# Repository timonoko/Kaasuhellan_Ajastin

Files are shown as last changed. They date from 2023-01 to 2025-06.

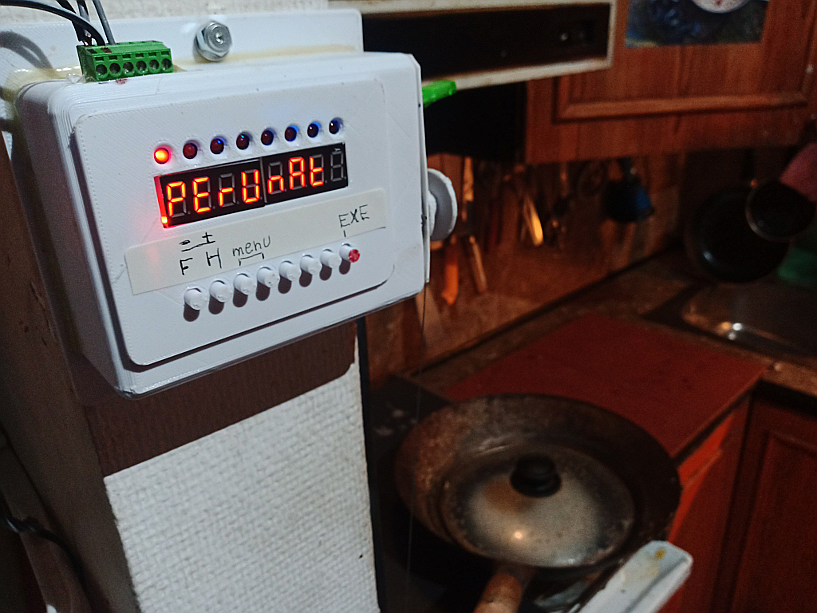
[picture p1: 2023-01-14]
Perunat.png

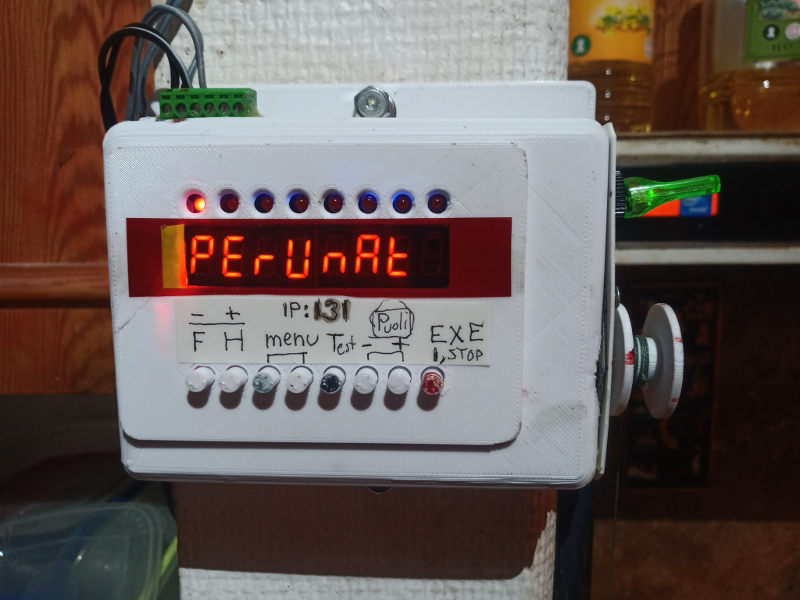
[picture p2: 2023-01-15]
perunat2.png

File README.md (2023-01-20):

# Kaasuhellan_Ajastin

ESP32-vehje kelaa siimalla vipuvarren päässä olevaa lieden pääkatkaisinta. Säätää
myös puoliliekin.

Havaitsee palohälytyksen, koska palohälyttimessä oleva transistori vetää
kun kaijuttimesta tulee ääntä.

Vehkeessä on myös eri ruokalajeille viritetty menyy.

Askelmoottori on entisestä skannerista ja näyttönappimoduuli on TM1638.

Mitään raja-antureita ei ole, sillä kun virrat katkaistaan, painovoima vetää rullauskelan takasin nolla-asentoon.
Kytkin myös A4988:n enable-pinnin, niin että toiminnan alussa vipua nostetaan 50 pykälää ja annetaan
sen jälkeen vapaasti pudota, jolloin nollaus on tarkka.

Hellan yläpuolella oleva lämpömittari TMP36GT9Z sammuttaa hanan, jos lämpötila on yli MAX_TEMP -- tai kun keittämistaä on kestänyt yli 3 minuuttia ja lämpötila on silti alle MIN_TEMP.

https://youtu.be/Kd3liw780tA

<image src=xstop.png>
<image src=Perunat.png>

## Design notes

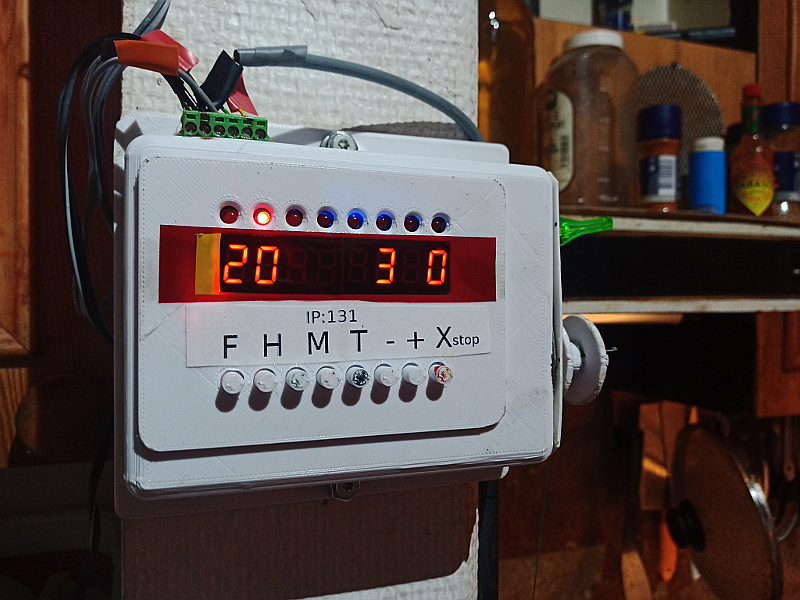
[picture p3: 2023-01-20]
xstop.png

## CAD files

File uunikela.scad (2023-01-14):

$fn=100;

difference(){
  cylinder(d=30,h=14);
  translate([0,0,-1])cylinder(d=7.2,h=17);
   translate([0,0,2]) difference(){
    cylinder(d=32,h=10);
    translate([0,0,-1])cylinder(d=12,h=17);
   }
}

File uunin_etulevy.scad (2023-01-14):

include <roundedcube.scad>


$fn=80;
thei=6.5;
module tappi(th) {
  difference(){
    cylinder(d=5.5,h=th);
    translate([0,0,-1]) cylinder(d=2.5,h=10+th);
  }
}
module etulevy () {
  difference() {
  translate([-10,-10,0])cube([76.5+20,50+20,2]);
  //  cube([76.5,50,2]);
  for (x=[10.5:56/7:67])translate([x,50-3.5,-1])cylinder(d1=3,d2=8,h=4);
  for (x=[11.2:54.45/7:67])translate([x,5.8,-1])cylinder(d=6,h=4);
  translate([6.5,27,-1]) cube([63,15,4]);
  translate([1,11,-1])  cube([3,13,2.5]);
  }
  translate([4,5,-thei])tappi(thei);
  translate([76.5-4,5,-thei])tappi(thei);
  translate([4,50-4.5,-thei])tappi(thei);
  translate([76.5-4,50-4.5,-thei])tappi(thei);
}


module nappaimet () { 
  for (x=[11.2:54.45/7:67])translate([x,5.8,0])cylinder(d=5,h=8);
  for (x=[11.2:54.45/7:67])translate([x,5.8,0])cylinder(d=7,h=1);
  for (x=[11.2:54.45/7:67])translate([x-2,5.8,0])cube([4,20,1]);
  translate([9,22,0])cube([60,5,1]);
}


module kotelo () {
  difference() {
    roundedcube([120,90,50],radius=6);
    translate([2,2,2])roundedcube([116,86,46],radius=4);
    translate([0,0,-1])cube([120,92,11]);
    translate([14,20,0]) cube([80,60,60]);
    translate([110,30,30])rotate([0,90,0])cylinder(d=36,h=20);
    translate([105,35,20])cube(18);
  }
  translate([4.5,4.5,12])tappi(35);
  translate([120-4.5,4.5,12])tappi(35);
  translate([120-4.5,90-4.5,12])tappi(35);
  translate([4.5,90-4.5,12])tappi(35);
}

module kansi () {
  difference() {
    union (){
      difference() {
	translate([2.3,2.3,0])roundedcube([115.4,85.4,46],radius=3.4);
	translate([0,0,-1])cube([120,92,5]);
	translate([0,0,7])cube([120,92,50]);
      }
      translate([0,0,-3])difference() {
	translate([-5,-15,0])roundedcube([130,120,46],radius=3.4);
	translate([-10,-17,-1])cube([170,130,5]);
	translate([-10,-17,7])cube([170,130,50]);
      }
    }
    translate([4.5,4.5,-2])cylinder(d=3,h=10);
    translate([120-4.5,4.5,-2])cylinder(d=3,h=10);
    translate([120-4.5,90-4.5,-2])cylinder(d=3,h=10);
    translate([4.5,90-4.5,-2])cylinder(d=3,h=10);
    translate([8,8,-2])roundedcube([104,74,46],radius=4);
  }
}

//translate([-10,-10,2]) rotate([180,0,0]) color("RED") etulevy(); nappaimet();

//translate([16,25,50]) etulevy();
//kotelo();
kansi();

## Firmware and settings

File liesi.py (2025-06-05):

# Kaasukeittiön totaalinen haltuunotto (c) Tnoko 2023

import tm1638,time,machine
from machine import Pin

tm = tm1638.TM1638(stb=Pin(13), clk=Pin(14), dio=Pin(12))

palohaly=Pin(15,Pin.IN)

direction=Pin(27,Pin.OUT)
step=Pin(17,Pin.OUT)
stepable=Pin(5,Pin.OUT)

adc=machine.ADC(machine.Pin(33),atten=machine.ADC.ATTN_11DB)

def tempe1():
    return (adc.read()*2450/900)*100./4096-50.

TEMP=tempe1()

def tempera(): # Kohinainen lämpomittari, käytetään 10 otoksen keskiarvoa
    global TEMP
    TEMP=(99*TEMP+tempe1())/100
    return 24+int(TEMP)

tempera();tempera();tempera()

MIN_TEMP_ORIG=tempera()
if MIN_TEMP_ORIG>25: MIN_TEMP_ORIG=25
MIN_TEMP=MIN_TEMP_ORIG
MIN_TEMP_TIME=5
MAX_TEMP=45

tm.brightness(1)
UP=1
DOWN=0
SIJAINTI=0

def myscroll(x):
      tm.show('        ')
      if len(x)<9: tm.show(x)
      else:
        x='  '+x
        for i in range(0,len(x)-7):
             tm.show(x[i:(i+8)])
             time.sleep(0.2)

def kaasuhana(asento,speed=500):
    global SIJAINTI
    tm.brightness(7)
    steps=asento-SIJAINTI
    if steps==0: return
    if steps<0: suunta=DOWN
    else: suunta=UP
    print('steps,suunta=',steps,suunta)
    direction.value(suunta)
    for x in range(abs(steps)):
        if suunta==UP: SIJAINTI+=1
        else: SIJAINTI-=1
        tm.number(SIJAINTI)
        tm.leds(x)
        step.value(1)
        time.sleep(1/speed)
        step.value(0)
        time.sleep(1/speed)
#    time.sleep(1)
    tm.brightness(1)
    with open('SIJAINTI.TXT', 'w') as f:  f.write('%d' % SIJAINTI)

from MENYY import menyy

def valinta(v):
    time.sleep(0.2)
    while True:
        tm.leds(2**v)
        myscroll(menyy[v][0])
        while True:
            k=tm.keys()
            if k>0:
                break
        time.sleep(0.3)
        if k==2**3:
            v=v+1
            if v==len(menyy):
                v=0
        if k==2**2:
            v=v-1
            if v<0:
                v=len(menyy)-1
        if k==2**7:
            break
    return v

def keys01(k):
    global aika1,aika2
    if k==2**0:
        if aika1==0:  aika1=1
        else: aika1=round(aika1*1.5)
        if aika1>500:  aika1=0
    if k==2**1:
        if aika2==0: aika2=1
        else: aika2=round(aika2*1.5)
        if aika2>500: aika2=0
    cou=0
    while tm.keys()>0:
        time.sleep(0.1)
        cou+=1
        if cou>3:
            if k==2**0: aika1=1
            if k==2**1: aika2=0

def hienosaato(k):  # Puoliliekin hienosäätö
    global PUOLI
    if k==2**5: PUOLI-=1
    else: PUOLI+=1
    puoli()
    tm.number(PUOLI)
    with open('PUOLI.TXT', 'w') as f:
        f.write('%d' % PUOLI)
    time.sleep(1)

def showtime (aika1, aika2):
    s=str(aika1)+" "+str(aika2)
    if MIN_TEMP==tempera(): s="E "+s
    elif MIN_TEMP>tempera(): s="- "+s
    while len(s)<6: s=" "+s
    tm.show(str(tempera())+s)

VIESTI=""
def keitto(kypalla): 
    global AIKA,MIN_TEMP_TIME,aika1,aika2,MIN_TEMP,VIESTI
    if kypalla: minsaa=aika1
    else: minsaa=aika2
    while minsaa > 0:
        for y in range(6):
            if y==4 and MIN_TEMP==100:  myscroll("SAMMUTA KATTILA")
            for z in range(10):
                tm.leds(0)
                tm.led(y+1,1)
                if kypalla: aika1=minsaa
                else: aika2=minsaa
                showtime(aika1,aika2)
                if palohaly.value()==0: aika2=0; VIESTI="SAVUA "; return
                if tempera()>MAX_TEMP: aika2=0; VIESTI="YLILAMPO"; return 
                if AIKA>MIN_TEMP_TIME and tempera()<MIN_TEMP: aika2=0; VIESTI="ALILAMPO"; return
                for cnt in range(10):
                    time.sleep(0.1)
                    if cnt==0:   tm.led(7,1); tm.led(0,0)
                    elif cnt==3: tm.led(7,0); tm.led(0,1)
                    elif cnt==6: tm.led(7,0); tm.led(0,0)
                    k=tm.keys()
                    if k==2**0 or k==2**1:
                        keys01(k)
                        if kypalla: minsaa=aika1
                        else: minsaa=aika2
                    if k==2**5 or k==2**6: hienosaato(k)
                    if k==2**7: return
        minsaa-=1
        AIKA+=1
        print("AIKA,MIN_TEMP_TIME,MIN_TEMP,tempera()=",AIKA,MIN_TEMP_TIME,MIN_TEMP,tempera())
    return 0

TAPISSA=500
with open('PUOLI.TXT') as file: PUOLI = int(file.read())

def taysi():
    kaasuhana(TAPISSA)

def puoli():  # Puoliliekin kohtaa pitää lähestyä varoen ettei liekki sammu
    kaasuhana(PUOLI+100)
    kaasuhana(PUOLI,80)

def nolla():
    kaasuhana(-1) 

# Nostetaan hanaa ylös ja annetaan sen vapaasti pudota ==> Nollakohta

with open('SIJAINTI.TXT') as file:  SIJAINTI = int(file.read())
if SIJAINTI!=-1: SIJAINTI=30 # tähän asentoon se putoaa kun virta katkeaa
kaasuhana(0)
stepable.value(0) 
kaasuhana(100)
stepable.value(1)
kaasuhana(0)
stepable.value(0)
kaasuhana(-1) # naru löysälle, ettei veny

AIKA=0
def keita():
    global AIKA,MIN_TEMP_TIME,aika1,aika2,MIN_TEMP
    if aika1>10 and aika2==0: # Uunissa on oma liekinvarmistin
        tm.show('  UUNI  ')
        MIN_TEMP_TIME=aika1+2 # Loppuviesti "ALILAMPO" jos sama
        MIN_TEMP=100
    else:
        tm.show(' KATTILA')
        MIN_TEMP_TIME=5
        MIN_TEMP=MIN_TEMP_ORIG
    while tm.keys()>0: pass
    if MIN_TEMP==100:
        while tm.keys()==0: myscroll("SAMMUTA KATTILA")
    AIKA=0
    taysi()
    keitto(kypalla=True)
    aika1=0
    if aika2==0:
        nolla()
        return
    puoli()
    keitto(kypalla=False)
    if aika1>0: keita() #uusiks
    aika2=0
    nolla()

aika1=2
aika2=0
valo=1

while True:
    time.sleep(0.1)
    k=tm.keys()
    tm.leds(2**valo)
    if k>0:
        valo=(valo+1)%8
        time.sleep(0.5)
    if VIESTI != "":
        tm.brightness(7)
        tm.show(VIESTI)
        time.sleep(1)
        tm.show("        ")
        time.sleep(1)
    else:
        showtime(aika1,aika2)
    if k==2**0 or k==2**1: # Keittoajat käsin
        keys01(k)
    if k==2**2 or k==2**3: # Keittoajat Menyystä
        v=valinta(0)
        aika1=menyy[v][1]
        aika2=menyy[v][2]
        keita() # Käynnistä Keittäminen Oitis
    if k==2**4:            # Kaasuhanan Testaus
        if SIJAINTI==TAPISSA: puoli()
        else: taysi()
    if k==2**5 or k==2**6: # Puoliliekin hienosäätö
        hienosaato(k)
    if k==2**7: # Käynnistä Keittäminen Oitis
        keita()

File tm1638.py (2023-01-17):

# MicroPython TM1638 LED display driver for 8x 7-segment decimal LED modules with 8x individual LEDs and 8x switches
# 8x push buttons

from micropython import const
from machine import Pin
from time import sleep_us, sleep_ms

print('HEEELO')

TM1638_CMD1 = const(64)  # 0x40 data command
TM1638_CMD2 = const(192) # 0xC0 address command
TM1638_CMD3 = const(128) # 0x80 display control command
TM1638_DSP_ON = const(8) # 0x08 display on
TM1638_READ = const(2)   # 0x02 read key scan data
TM1638_FIXED = const(4)  # 0x04 fixed address mode

# 0-9, a-z, blank, dash, star
_SEGMENTS = bytearray(b'\x3F\x06\x5B\x4F\x66\x6D\x7D\x07\x7F\x6F\x77\x7C\x39\x5E\x79\x71\x3D\x76\x06\x1E\x7A\x38\x37\x54\x3F\x73\x67\x50\x6D\x78\x3E\x1C\x2A\x76\x6E\x5B\x00\x40\x63')

class TM1638(object):
    """Library for the TM1638 LED display driver."""
    def __init__(self, stb, clk, dio, brightness=7):
        self.stb = stb
        self.clk = clk
        self.dio = dio

        if not 0 <= brightness <= 7:
            raise ValueError("Brightness out of range")
        self._brightness = brightness

        self._on = TM1638_DSP_ON

        self.clk.init(Pin.OUT, value=1)
        self.dio.init(Pin.OUT, value=0)
        self.stb.init(Pin.OUT, value=1)

        self.clear()
        self._write_dsp_ctrl()

    def _write_data_cmd(self):
        # data command: automatic address increment, normal mode
        self._command(TM1638_CMD1)

    def _set_address(self, addr=0):
        # address command: move to address
        self._byte(TM1638_CMD2 | addr)

    def _write_dsp_ctrl(self):
        # display command: display on, set brightness
        self._command(TM1638_CMD3 | self._on | self._brightness)

    def _command(self, cmd):
        self.stb(0)
        self._byte(cmd)
        self.stb(1)

    def _byte(self, b):
        for i in range(8):
            self.clk(0)
            self.dio((b >> i) & 1)
            self.clk(1)

    def _scan_keys(self):
        """Reads one of the four bytes representing which keys are pressed."""
        pressed = 0
        self.dio.init(Pin.IN, Pin.PULL_UP)
        for i in range(8):
            self.clk(0)
            if self.dio.value():
                pressed |= 1 << i
            self.clk(1)
        self.dio.init(Pin.OUT)
        return pressed

    def power(self, val=None):
        """Power up, power down or check status"""
        if val is None:
            return self._on == TM1638_DSP_ON
        self._on = TM1638_DSP_ON if val else 0
        self._write_dsp_ctrl()

    def brightness(self, val=None):
        """Set the display brightness 0-7."""
        # brightness 0 = 1/16th pulse width
        # brightness 7 = 14/16th pulse width
        if val is None:
            return self._brightness
        if not 0 <= val <= 7:
            raise ValueError("Brightness out of range")
        self._brightness = val
        self._write_dsp_ctrl()

    def clear(self):
        """Write zeros to each address"""
        self._write_data_cmd()
        self.stb(0)
        self._set_address(0)
        for i in range(16):
            self._byte(0x00)
        self.stb(1)

    def write(self, data, pos=0):
        """Write to all 16 addresses from a given position.
        Order is left to right, 1st segment, 1st LED, 2nd segment, 2nd LED etc."""
        if not 0 <= pos <= 15:
            raise ValueError("Position out of range")
        self._write_data_cmd()
        self.stb(0)
        self._set_address(pos)
        for b in data:
            self._byte(b)
        self.stb(1)

    def led(self, pos, val):
        """Set the value of a single LED"""
        self.write([val], (pos << 1) + 1)

    def leds(self, val):
        """Set all LEDs at once. LSB is left most LED.
        Only writes to the LED positions (every 2nd starting from 1)"""
        self._write_data_cmd()
        pos = 1
        for i in range(8):
            self.stb(0)
            self._set_address(pos)
            self._byte((val >> i) & 1)
            pos += 2
            self.stb(1)

    def segments(self, segments, pos=0):
        """Set one or more segments at a relative position.
        Only writes to the segment positions (every 2nd starting from 0)"""
        if not 0 <= pos <= 7:
            raise ValueError("Position out of range")
        self._write_data_cmd()
        for seg in segments:
            self.stb(0)
            self._set_address(pos << 1)
            self._byte(seg)
            pos += 1
            self.stb(1)

    def keys(self):
        """Return a byte representing which keys are pressed. LSB is SW1"""
        keys = 0
        self.stb(0)
        self._byte(TM1638_CMD1 | TM1638_READ)
        for i in range(4):
            keys |= self._scan_keys() << i
        self.stb(1)
        return keys

    def encode_digit(self, digit):
        """Convert a character 0-9, a-f to a segment."""
        return _SEGMENTS[digit & 0x0f]

    def encode_string(self, string):
        """Convert an up to 8 character length string containing 0-9, a-z,
        space, dash, star to an array of segments, matching the length of the
        source string excluding dots, which are merged with previous char."""
        segments = bytearray(len(string.replace('.','')))
        j = 0
        for i in range(len(string)):
            if string[i] == '.' and j > 0:
                segments[j-1] |= (1 << 7)
                continue
            segments[j] = self.encode_char(string[i])
            j += 1
        return segments

    def encode_char(self, char):
        """Convert a character 0-9, a-z, space, dash or star to a segment."""
        o = ord(char)
        if o == 32:
            return _SEGMENTS[36] # space
        if o == 42:
            return _SEGMENTS[38] # star/degrees
        if o == 45:
            return _SEGMENTS[37] # dash
        if o >= 65 and o <= 90:
            return _SEGMENTS[o-55] # uppercase A-Z
        if o >= 97 and o <= 122:
            return _SEGMENTS[o-87] # lowercase a-z
        if o >= 48 and o <= 57:
            return _SEGMENTS[o-48] # 0-9
        raise ValueError("Character out of range: {:d} '{:s}'".format(o, chr(o)))

    def hex(self, val):
        """Display a hex value 0x00000000 through 0xffffffff, right aligned, leading zeros."""
        string = '{:08x}'.format(val & 0xffffffff)
        self.segments(self.encode_string(string))

    def number(self, num):
        """Display a numeric value -9999999 through 99999999, right aligned."""
        # limit to range -9999999 to 99999999
        num = max(-9999999, min(num, 99999999))
        string = '{0: >8d}'.format(num)
        self.segments(self.encode_string(string))

    #def float(self, num):
    #    # needs more work
    #    string = '{0:>9f}'.format(num)
    #    self.segments(self.encode_string(string[0:9]))
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
